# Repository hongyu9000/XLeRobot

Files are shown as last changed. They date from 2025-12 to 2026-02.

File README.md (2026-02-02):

# [XLeRobot 🤖](https://xlerobot.readthedocs.io/en/latest/index.html)




<a href="https://xlerobot.readthedocs.io/en/latest/index.html">
  front
</a>





---

**🚀 Bringing Embodied AI to Everyone - Cheaper Than an iPhone! 📱**  
**💵 Starts from $660 cost and ⏰ <4hrs total assembly time!!**

*Built upon the giants: [LeRobot](https://github.com/huggingface/lerobot), [SO-100/SO-101](https://github.com/TheRobotStudio/SO-ARM100), [Lekiwi](https://github.com/SIGRobotics-UIUC/LeKiwi), [Bambot](https://github.com/timqian/bambot)*

<table>
  <tr>
    <td></td>
    <td></td>
    <td></td>
  </tr>
  <tr>
    <td></td>
    <td></td>
    <td></td>
  </tr>
  <tr>
    <td></td>
    <td></td>
    <td></td>
  </tr>
</table>

---

# 📰 News 
- 2026-1-29: Play with XLeRobot directly in browser with Mujoco and 3DGS: https://vector-wangel.github.io/MuJoCo-GS-Web/
  - 
- 2025-12-02: [Dual-wheel version released](https://xlerobot.readthedocs.io/en/latest/hardware/getting_started/assemble_2wheel.html)! Have a more stable and accurate differential-wheel base for a cheaper price. (Default servo motor, optional scooter brushless Motor available at a similar price)
  

- 2025-11-11: **[Temporary VLA tutorial](https://xlerobot.readthedocs.io/en/latest/software/getting_started/RL_VLA.html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)** out. Official version out soon.
- 2025-09-22: **Hardware Assembly Video Tutorial** availabe at [Youtube](https://www.youtube.com/watch?v=upB1CEFeOlk) and [Bilibili](https://www.bilibili.com/video/BV1AGWFzUEJf/). Thanks WOWROBO for making this video!
- 2025-09-09: **Developer Assembly kit (excluding battery and IKEA cart) ready for purchase** in [China (Taobao) for **3699￥**](https://e.tb.cn/h.SZFbBgZABZ8zRPe?tk=ba514rTBRjQ) and [world-wide for **579\$**](https://shop.wowrobo.com/products/xlerobot-dual-arm-mobile-household-robot-kit?variant=47297659961561). _(In collaboration with **Wowrobo**)_
  - Non-profit, I personally don't earn any from this. I also asked Wowrobo to set the price as low as possible.
  - This is only the assembly kit for developers, please check documentation website and this repo for available codes and tutorials before you purchase.
- 2025-09-09: Joined [Embodied AI Home Robot Hackathon](https://www.seeedstudio.com/embodied-ai-worldwide-hackathon-home-robot.html) (Oct 25–26, Bay Area) held by **SEEED x Nvidia x Huggingface** as mentor! [Register HERE](https://docs.google.com/forms/d/e/1FAIpQLSdYYDegdgIypxuGJNLcoc8kbdmU4jKgl49zg4X-107LAmBN4g/viewform).

- 2025-08-30: XLeRobot 0.3.0 Release with final outfit touch up and household chores showcase demos. 

- 2025-07-30: [Control XLeRobot in real life](https://xlerobot.readthedocs.io/en/latest/software/index.html) with **keyboard/Xbox controller/Switch joycon** in the wild anywhere. All bluetooth, no wifi needed and zero latency.

- 2025-07-08: [**Simulation**](https://xlerobot.readthedocs.io/en/latest/simulation/index.html) with updated urdfs, control scripts (support Quest3 VR, keyboard, Xbox controller, switch joycon), support for new hardware and cameras, RL environment. Get started in 15 min.
-  vr

- 2025-07-01: [**Documentation** website](https://xlerobot.readthedocs.io/en/latest/index.html) out for more orgainized tutorials, demos and resources.

- 2025-06-13: [**XLeRobot 0.2.0**](https://xlerobot.readthedocs.io) hardware setup, the 1st version fully capable for autonomous household tasks, starts from 660$. 

---

## 💵 Total Cost 💵

> [!NOTE] 
> Cost excludes 3D printing, tools, shipping, and taxes.

| Price (Buy all the parts yourself) | US | EU | CN | IN |
| --- | --- | --- | --- | --- |
| **Basic** (use your laptop, single RGB head cam) | **~$660** | **~€680** | **~¥3999** | **~₹87000** |
| ↑ Stereo dual-eye RGB head cam | +$30 | +€30 | +¥199 | +₹6550 |
| + RasberryPi | +$79 | +€79 | +¥399 | +₹7999 |
| ↑ RealSense RGBD head cam | +$220 | +€230 | +¥1499 | +₹35726 |

---
## 🚀 Get Started 🚀

> [!NOTE] 
> If you are totally new to programming, please spend at least a day to get yourself familiar with basic Python, Ubuntu and Github (with the help of Google and AI). At least you should know how to setup ubuntu system, git clone, pip install, use intepreters (VS Code, Cursor, Pycharm, etc.) and directly run commands in the terminals.

1. 💵 **Buy your parts**: [Bill of Materials](https://xlerobot.readthedocs.io/en/latest/hardware/getting_started/material.html)
2. 🖨️ **Print your stuff**: [3D printing](https://xlerobot.readthedocs.io/en/latest/hardware/getting_started/3d.html)
3. 🔨 ~~Avengers~~: [**Assemble**!](https://xlerobot.readthedocs.io/en/latest/hardware/getting_started/assemble.html)
4. 💻 **Software**: [Get your robot moving!](https://xlerobot.readthedocs.io/en/latest/software/index.html)

---

## Contribute

**👋 Want to contribute to XLeRobot?**
Please refer to [CONTRIBUTING.md](CONTRIBUTING.md) for guidance on how to get involved!

**Main Contributors**

- [Gaotian/Vector Wang](https://vector-wangel.github.io/)
- [Jiahao Wang](https://github.com/kahowang), [Chunbo Pan](https://github.com/IIMFINE), [QiLiu](https://github.com/Lakesenberg), [Isaac Sin](https://github.com/IsaacSinn), [Ryan Chan](https://github.com/RapidCAMO): [MakerMods team](https://www.makermods.ai/), VLA and VR integration
- [Zhuoyi Lu](https://lzhuoyi.github.io/Zhuoyi_Lu.github.io/): RL sim2real deploy, teleop on real robot (Xbox, VR, Joycon)
- Yiyang Huang: RL & VLA implementation (ongoing)
- YCP: WebUI for remote control (ongoing)
- [Lixing Zhang](lixingzhang.com): Hardware design improvements
- Nicole Yue: Documentation website setup
- Yuesong Wang: Mujoco simulation
- 

This is just a small brick in the pyramid, made possible by [LeRobot](https://github.com/huggingface/lerobot), [SO-100](https://github.com/TheRobotStudio/SO-ARM100), [Lekiwi](https://github.com/SIGRobotics-UIUC/LeKiwi), and [Bambot](https://github.com/timqian/bambot). Thanks to all the talented contributors behind these detailed and professional projects.

Looking forward to collaborating with anyone interested in contributing to this project!

## About me

[Gaotian/Vector Wang](https://vector-wangel.github.io/)

I am a CS graduate student at Rice University [RobotPi Lab](https://robotpilab.github.io/), focusing on robust object manipulation, where we propse virtual cages and funnels and physics-aware world models to close the Sim2real gap and achieve robust manipulation under uncertainties. One of my papers, Caging in Time, has recently been accepted by International Journal of Robotics Research (IJRR).

I built XLeRobot as a personal hobby to instantiate my research theory, also to provide a low-cost platform for people who are interested in robotics and embodied AI to work with. 

---

## Citation

If you want, you can cite this work with:

```bibtex
@misc{wang2025xlerobot,
    author = {Wang, Gaotian and Lu, Zhuoyi and Yiyang, Huang and Yihao, Liu},
    title = {XLeRobot: A Practical Low-cost Household Dual-Arm Mobile Robot Design for General Manipulation},
    howpublished = "\url{https://github.com/Vector-Wangel/XLeRobot}",
    year = {2025}
}
```
---Generated Image August 27, 2025 - 4_58PM

## 🪧 Disclaimer 🪧

> [!NOTE]
> If you build, buy, or develop a XLeRobot based on this repo, you will be fully responsible for all the physical and mental damages it does to you or others.

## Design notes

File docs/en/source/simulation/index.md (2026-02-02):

# Simulation

##### Web Mujoco simulation

Play with XLeRobot instantly on web, using mujoco engine and 3DGS. See detailed instruction [HERE](https://github.com/Vector-Wangel/MuJoCo-GS-Web)

<iframe 
    src="https://vector-wangel.github.io/MuJoCo-GS-Web/" 
    width="100%" 
    height="600px"
    style="border: none; border-radius: 8px;"
    allowfullscreen>
</iframe>

##### [👋 Get Started](getting_started/index)

- [A short technical blog](https://vectorwang.notion.site/Analytical-IK-for-SO101-20abb280f59380d288bcdd398ffbfab1) for analytical IK introduction.

- A detailed [**Step-by-step Installation Guide**](getting_started/index) that can get you started to replicate this demo in 10 min.

- URDF files, maniskill robot agent scripts, joint/EE control scripts.

##### [👀 VR Control](getting_started/vr_sim)

<video width="100%" style="max-width: 100%;" controls>
  <source src="https://vector-wangel.github.io/XLeRobot-assets/videos/Sim_demos/XLeRobot_0_2_3.mp4" type="video/mp4">
  Your browser does not support the video tag.
</video>

##### [🔩 More Scenes](getting_started/simdemos)

<video width="100%" style="max-width: 100%;" controls>
  <source src="https://vector-wangel.github.io/XLeRobot-assets/videos/Sim_demos/XLeRobot_0_1_5.mp4" type="video/mp4">
  Your browser does not support the video tag.
</video>

```{toctree}
getting_started/index
getting_started/vr_sim
getting_started/simdemos
```

<!-- ```{toctree}
:maxdepth: 1

control/index
table_top_gripper/index
quadruped/index
humanoid/index
mobile_manipulation/index
dextrous/index
digital_twins/index
drawing/index
external/index
``` -->

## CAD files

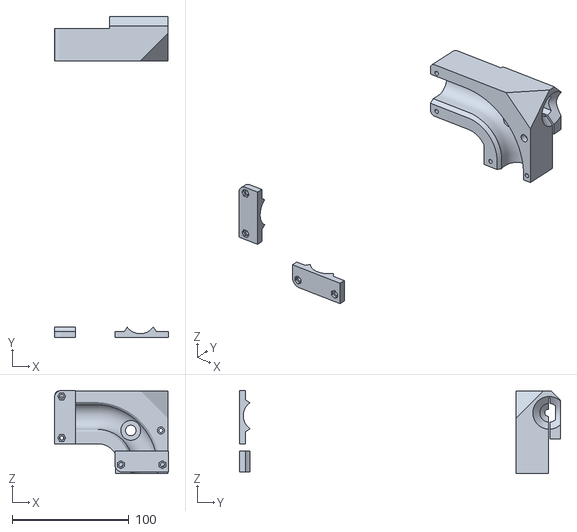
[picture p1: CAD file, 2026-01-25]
hardware/Brushlessmotor connector.stl
98.1 x 275.3 x 71.3

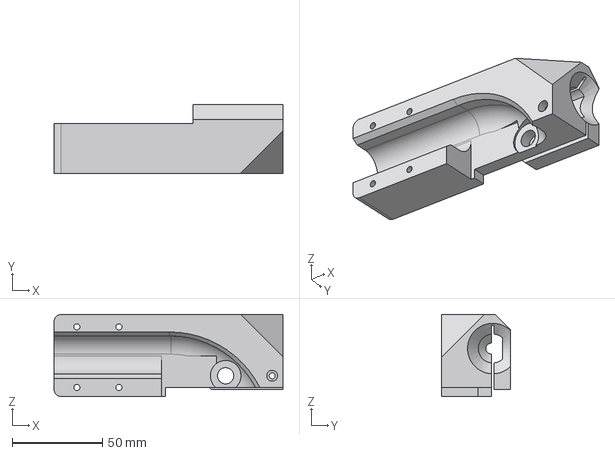
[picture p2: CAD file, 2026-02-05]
hardware/step/brushless_motor_base_holder.step
127.0 x 38.0 x 45.5 mm

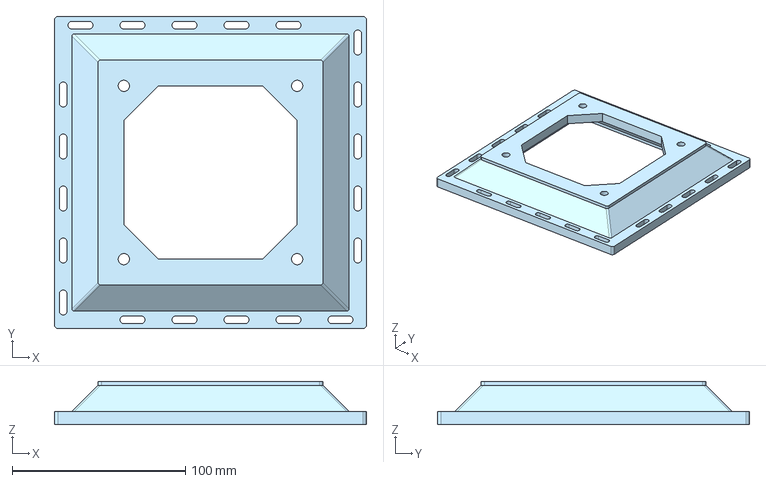
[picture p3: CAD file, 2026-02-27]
hardware/step/HighTorqueRobotics/ht_holder_single.step
180.0 x 180.0 x 25.0 mm

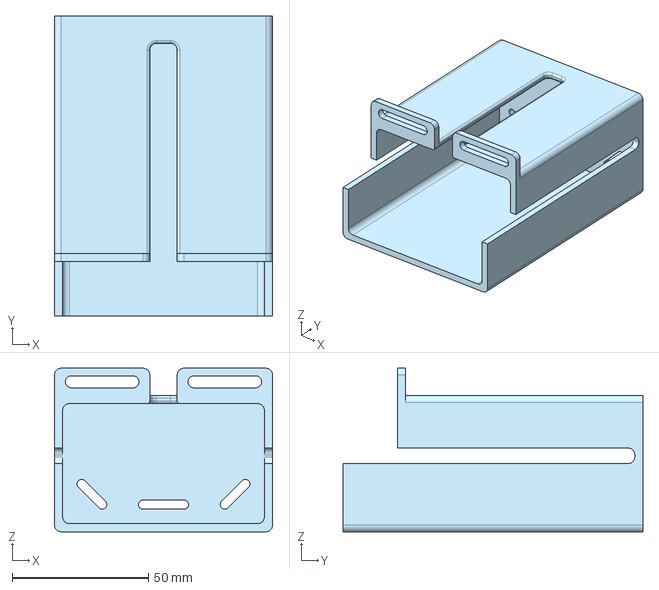
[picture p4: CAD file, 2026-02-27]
hardware/step/Misc/front_back_hub.step
80.0 x 110.0 x 60.0 mm

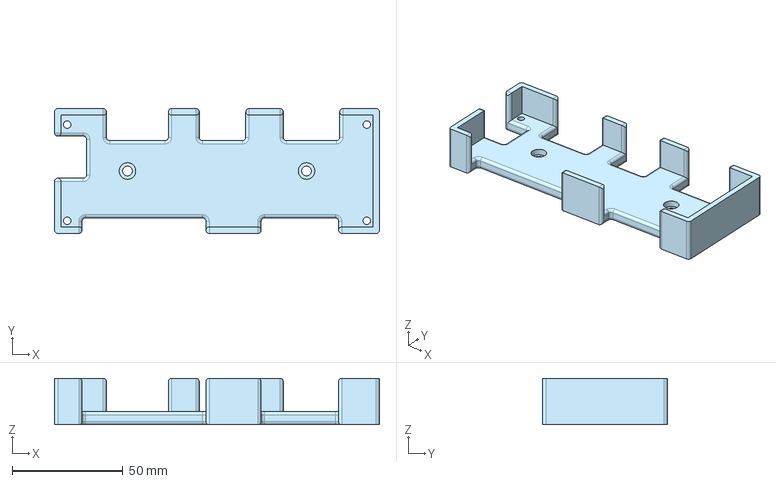
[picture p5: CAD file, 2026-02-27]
hardware/step/ODrive/odrive_cap.step
147.0 x 56.5 x 21.0 mm

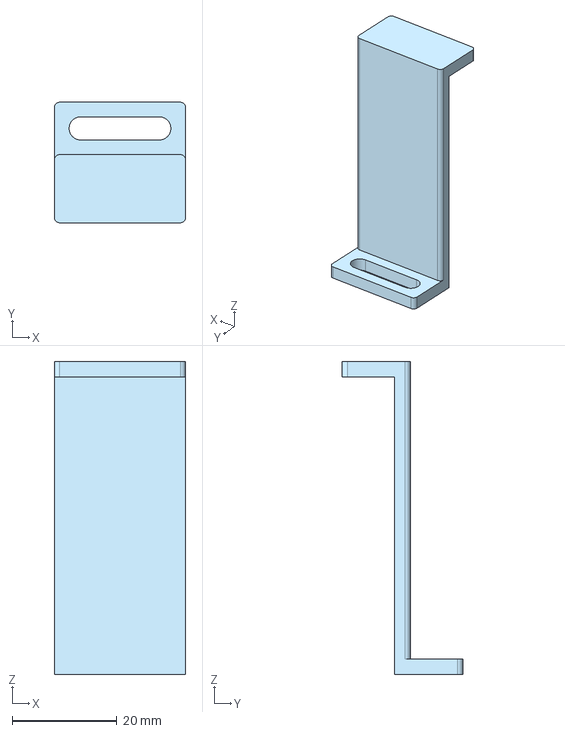
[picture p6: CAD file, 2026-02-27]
hardware/step/Thor/thor_holder_edge.step
25.0 x 23.0 x 59.7 mm

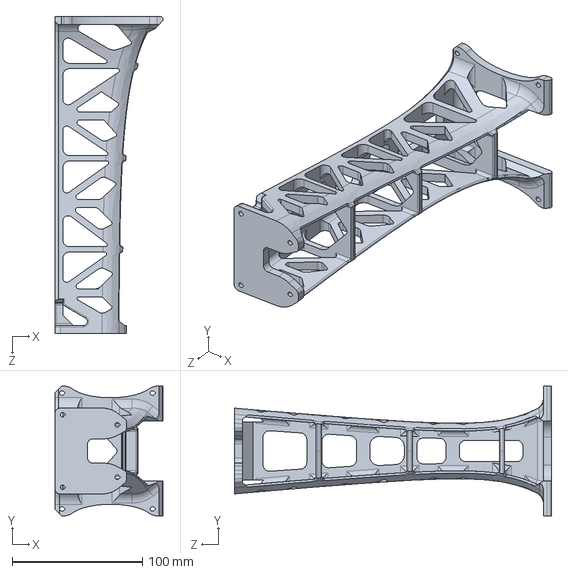
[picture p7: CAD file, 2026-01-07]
hardware/step/XLeRobot_040/XLeRobot040_neck_refined.step
83.1 x 99.8 x 243.8 mm

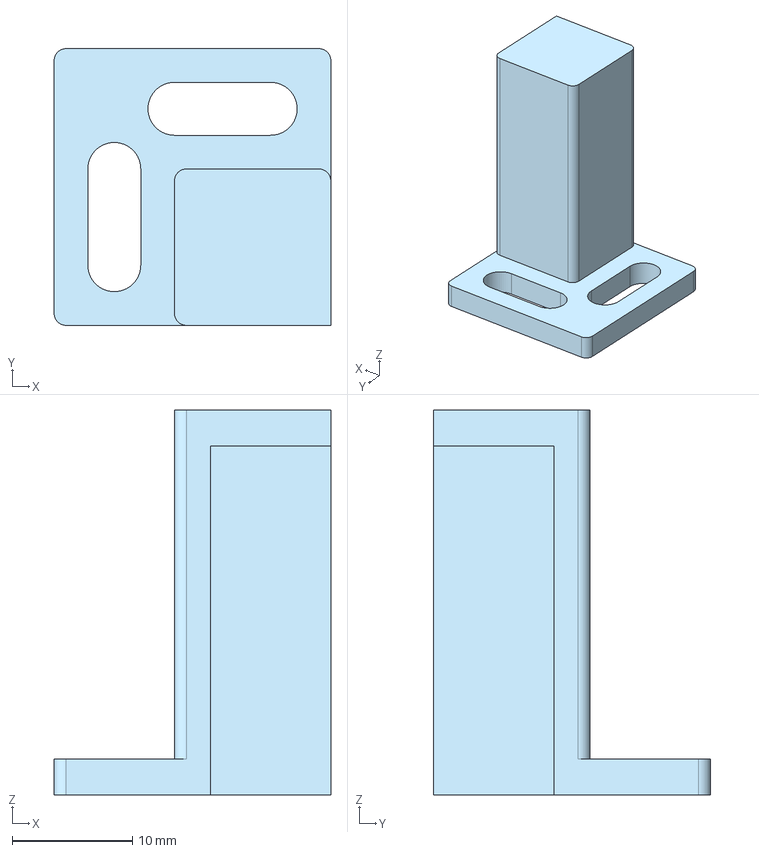
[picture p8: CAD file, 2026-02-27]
hardware/step/HighTorqueRobotics/ht_board_holder_corner.step
23.0 x 23.0 x 32.0 mm

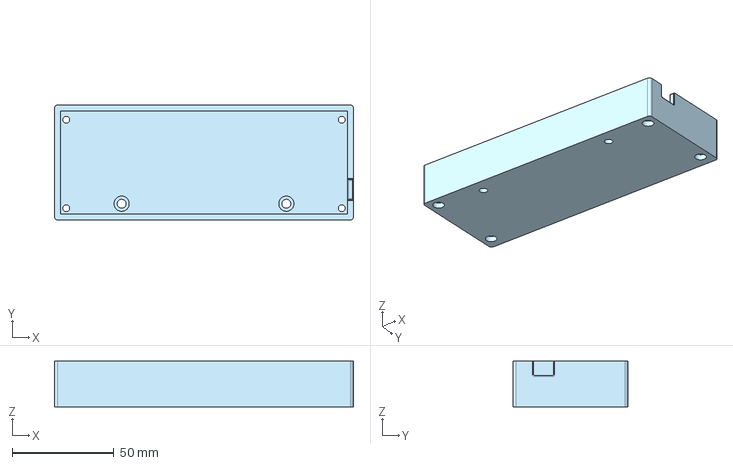
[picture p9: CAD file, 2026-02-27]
hardware/step/ODrive/odrive_housing.step
147.0 x 56.5 x 22.5 mm

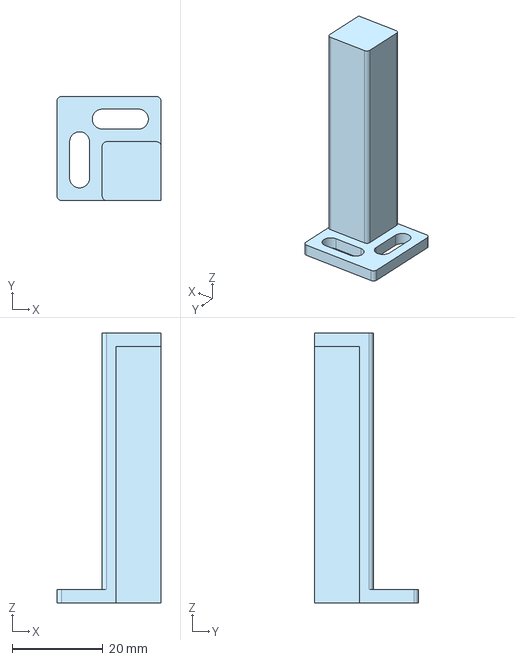
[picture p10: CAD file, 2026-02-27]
hardware/step/Thor/thor_holder_corner.step
23.0 x 23.0 x 59.7 mm

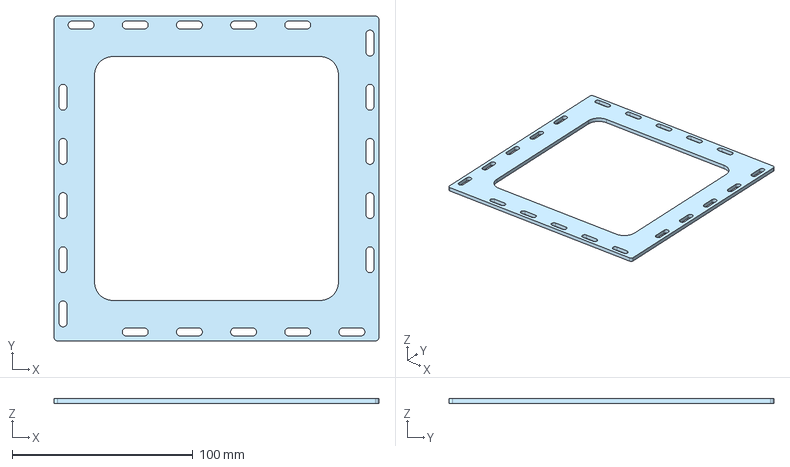
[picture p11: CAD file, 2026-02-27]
hardware/step/HighTorqueRobotics/ht_holder_single_bottom.step
180.0 x 180.0 x 3.00 mm

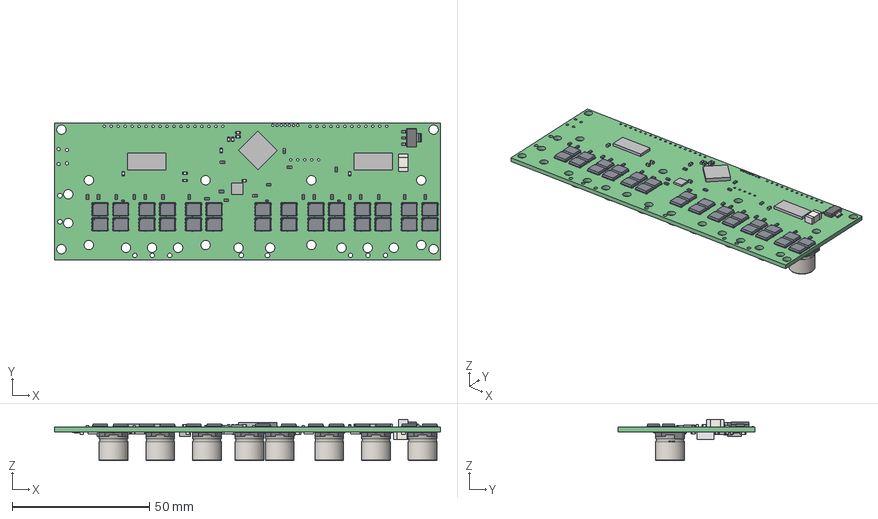
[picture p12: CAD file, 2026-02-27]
hardware/step/ODrive/PCB_v3.2.step
140.5 x 50.0 x 15.0 mm
Board
SOT23-5
Extruded x 201
RES_0402_(1005_metric) x 3
RES_0603_(1608_metric) x 48
SOT223-4
User_Library-DFN5x6_SO8FL_Extruded x 56
User_Library-DFN5x6_SO8FL_Extruded_2 x 56
User_Library-DFN5x6_SO8FL_Cylinder x 28
User_Library-DFN5x6_SO8FL_Extruded_3 x 28
User_Library-DFN5x6_SO8FL_Extruded_4 x 28
User_Library-DFN5x6_SO8FL_Extruded_5 x 112
User_Library-DFN5x6_SO8FL_Extruded_6 x 28
CAP_Alum_Elec_Size_G x 8

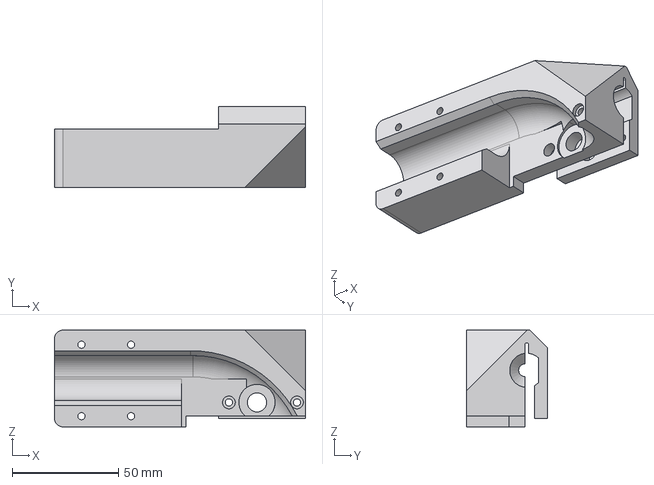
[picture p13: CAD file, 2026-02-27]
hardware/step/ODrive/odrive_motor_holder.step
118.0 x 38.0 x 45.5 mm

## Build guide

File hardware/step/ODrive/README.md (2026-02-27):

ODrive housing parts.

Dimensions retrieved from PCB v3.2.step by https://discourse.odriverobotics.com/t/housing-for-odrive-v3/97.

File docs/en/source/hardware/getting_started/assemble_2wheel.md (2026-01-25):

# Dual wheel Assembly

Here briefly introduce how to build the dual wheel version.

(This page is still under construction)

## Intro
Main changes compared to 0.3.0:

- Dual wheel: More stable, higher moving speed, better passability, and larger torque (compared to 3 omni-wheels). 2 verisons: servo motors and brushless motors.
- Improved top base design: modular arm base with changable arm installing directions. 360 degree and compact head design.  

This 0.4.0 version of XLeRobot is the last version that is fully based on Feetech servo motors and the SO101 chassis. After extensive testing and research, we realized the limitations of servo motors (speed, noise, payload, etc.), and we believe this hardware version offers the best balance among cost, ease of assembly, stability, and practicality.

Regarding a lifting (height-adjustable) base, we have also explored related designs, but the maintenance difficulty and stability issues make it hard to achieve a good solution using only servo motors. For most development scenarios, mobility at desk height is already sufficient to support initial research and development needs. We also found that adding more degrees of freedom increases the difficulty of data collection and hurts policy generalization.

Going forward, we plan to collaborate with Hightorque and wowrobo to build more product-level, low-cost, open-source mobile robots based on higher-performance motors.

Official Assembly Videos from Wowrobo:
<iframe width="800" height="600" 
    src="https://www.youtube.com/embed/4bXCFw57T60" 
    frameborder="0" 
    allowfullscreen>
</iframe>

<iframe width="800" height="600" 
    src="//player.bilibili.com/player.html?bvid=BV1JpiqBfEuf&autoplay=0" 
    frameborder="0" 
    allowfullscreen>
</iframe>

### Servo motor version

Pros: 
- Compared to previous version: more stable, control is more accurate, less wiggle
- Compared to brushless version: still same servo motors, easier wiring and control

Cons:
- Compared to previous version: lose one Dof of moving left and right
- Compared to brushless version: still same servo motors, noisy, speed and torque not very high.

This can already be purchased at wowrobo. 

You can also buy parts yourself, what you need besides 3D printed parts and servo motors:

- Universal walker wheels (5 inches)
- 30 x 37 x 4mm Bearings
- longer Motor cables (or extension kit)



Find STL file [Here](https://github.com/Vector-Wangel/XLeRobot/blob/main/hardware/XLeRobot_0_4_0_extra.stl)

Animation (19)
Animation (18)

Assembled picture:



### Brushless motor version

Build upon [Bracket Bot](https://www.bracket.bot/).

Find the connector to the IKEA cart [here](https://github.com/Vector-Wangel/XLeRobot/blob/main/hardware/Brushlessmotor%20connector.stl). (M8x20 screws required)

Pros: a fully stable and robust version with great performance.

Cons: more complex wiring.



Animation (20)

Still working on, release soon.

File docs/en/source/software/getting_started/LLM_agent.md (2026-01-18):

## LLM Agent Control

Imagine telling the robot "go cleanup my kitchen" and watching it doing so. This tutorial will show you how you can make your XLeRobot fully autonomous, self-decision making machine by providing it with LLM agent. An agent that uses camera vision and voice commands to move the robot and manipulate objects with VLA policies.

Demo of agent controlling XLeRobot, that has a task to grab a notebook and give it to human:

<video width="100%" controls>
  <source src="https://vector-wangel.github.io/XLeRobot-assets/videos/Real_demos/agent_in_action.mov" type="video/mp4">
  Your browser does not support the video tag.
</video>

### Getting Started

To create our agent, we will use the [RoboCrew](https://github.com/Grigorij-Dudnik/RoboCrew) library - one specially designed for embodied agents. On your control device (Raspberry Pi or laptop) create a new virtual environment and install it with:

```bash
pip install robocrew
```

Next, create the python script to control your robot. Let's start by creating a simple agent that performs just one hardcoded task and finishes. 

First, let's initialize camera and create tools for agent to control a wheel movement:

```python
from robocrew.core.camera import RobotCamera
from robocrew.core.LLMAgent import LLMAgent
from robocrew.robots.XLeRobot.tools import create_move_forward, create_turn_right, create_turn_left
from robocrew.robots.XLeRobot.servo_controls import ServoControler

# set up main camera
main_camera = RobotCamera("/dev/camera_center") # camera usb port Eg: /dev/video0

#set up servo controler
right_arm_wheel_usb = "/dev/arm_right"    # provide your right arm usb port. Eg: /dev/ttyACM1
servo_controler = ServoControler(right_arm_wheel_usb=right_arm_wheel_usb)

#set up tools
move_forward = create_move_forward(servo_controler)
turn_left = create_turn_left(servo_controler)
turn_right = create_turn_right(servo_controler)
```

in place of `/dev/arm_right` you should provide the USB port name of your right arm (one connected to the wheels).

Next, let's initialize and run an agent itself:

```python
# init agent
agent = LLMAgent(
    model="google_genai:gemini-3-flash-preview",
    tools=[
        move_forward,
        turn_left,
        turn_right,
    ],
    main_camera=main_camera,
    servo_controler=servo_controler,
)

agent.task = "Approach a human."

agent.go()
```

In the code above we initialized our agent with the maneuver tools we created earlier. You can provide any model in LangChain notation. Next, we hard-coding a task for our agent and running it.

Before going to LLM, camera image is specially augmented to make it easier for robot to understand its environment: 

<div style="text-align: center; font-style: italic">
  
  <p>That's how your robot sees the world.</p>
</div>

Also, create the `.env` file with parameter `GOOGLE_API_KEY=<your gemini api key here>` beside the script to connect to LLM.

Now run the code and watch your XLeRobot approaching you - then it will finish its work by calling `finish_task` tool!

Complete code is here:

```python
from robocrew.core.camera import RobotCamera
from robocrew.core.LLMAgent import LLMAgent
from robocrew.robots.XLeRobot.tools import create_move_forward, create_turn_right, create_turn_left
from robocrew.robots.XLeRobot.servo_controls import ServoControler

# set up main camera
main_camera = RobotCamera("/dev/camera_center") # camera usb port Eg: /dev/video0

#set up servo controler
right_arm_wheel_usb = "/dev/arm_right"    # provide your right arm usb port. Eg: /dev/ttyACM1
left_arm_head_usb = "/dev/arm_left"      # provide your left arm usb port. Eg: /dev/ttyACM0
servo_controler = ServoControler(right_arm_wheel_usb, left_arm_head_usb)

#set up tools
move_forward = create_move_forward(servo_controler)
turn_left = create_turn_left(servo_controler)
turn_right = create_turn_right(servo_controler)

# init agent
agent = LLMAgent(
    model="google_genai:gemini-3-flash-preview",
    tools=[move_forward, turn_left, turn_right],
    main_camera=main_camera,
    servo_controler=servo_controler,
)

agent.task = "Approach a human."

agent.go()
```

### Set up Udev rules

Before proceeding to more advanced examples, let's do optional, but highly recommended step - make the usb port names for arms and cameras constant, to avoid swapping those names after every Raspberry Pi reboot. To do it, we need to set up udev rules. Luckily, RoboCrew already contains an utility that makes a complicated process of setting up udevs a matter of few clicks.

Run:

```bash
robocrew-setup-usb-modules
```

Utility will ask you to disconnect all usbs and then connect one after another - that way your usb devices will receive a constant names.

### Voice-conrolled agent

We managed to run our simple agent, now let's give it an ability to listen to our voice commands through the microphone.

First, we need to install Portaudio, to enable our control device to hear:

```bash
sudo apt install portaudio19-dev
```

Connect to your agent a soundcard with microphone, and optionally speaker, if you want robot to respond to you.

Let's change the agent initialization a little bit:

```python
agent = LLMAgent(
    model="google_genai:gemini-3-flash-preview",
    tools=[move_forward, turn_left, turn_right],
    main_camera=main_camera,
    servo_controler=servo_controler,
    sounddevice_index=2,    # provide your microphone device index.
    wakeword="hey robot",   # optional - set up custom wakeword (default is "robot")
    tts=True,               # enable text-to-speech (robot can speak).
)

agent.go()
```

As you can see, we need to provide index of our soundcard with microphone. We can also set up a wakeword (default is "robot") - when robot hears that word in your sentence, it treats sentence as a new task; otherwise ignores it.

`tts=True` is needed if you want robot to speak.

We can also set up `history_len` - how many of last movements robot should keep in the memory, to avoid memory overflow.

Run the code and ask the robot to go somewhere!

Complete code is here:

```python
from robocrew.core.camera import RobotCamera
from robocrew.core.LLMAgent import LLMAgent
from robocrew.robots.XLeRobot.tools import create_move_forward, create_turn_right, create_turn_left
from robocrew.robots.XLeRobot.servo_controls import ServoControler

# set up main camera
main_camera = RobotCamera("/dev/camera_center") # camera usb port Eg: /dev/video0

#set up servo controler
right_arm_wheel_usb = "/dev/arm_right"    # provide your right arm usb port. Eg: /dev/ttyACM1
servo_controler = ServoControler(right_arm_wheel_usb=right_arm_wheel_usb)

#set up tools
move_forward = create_move_forward(servo_controler)
turn_left = create_turn_left(servo_controler)
turn_right = create_turn_right(servo_controler)

# init agent
agent = LLMAgent(
    model="google_genai:gemini-3-flash-preview",
    tools=[move_forward, turn_left, turn_right],
    main_camera=main_camera,
    servo_controler=servo_controler,
    sounddevice_index=2,    # provide your microphone device index.
    wakeword="hey robot",   # optional - set up custom wakeword (default is "robot")
    tts=True,               # enable text-to-speech (robot can speak).
)

agent.task = "Wait for the voice commands and execute."

agent.go()
```

### Activate arm manipulation

Let's go to the most advanced and useful part of our agent - the arms manipulation through VLA policies! That allows the robot to make full range of household tasks - like throwing out a trash or bringing you a tea from kitchen.

First of all, you need to train the policy agent will utilize later. Reference [VLA tutorial](https://xlerobot.readthedocs.io/en/latest/software/getting_started/VLA_ACT.html) to learn how to do it.

Let's assume you trained VLA policy that grabs a notebook from the table and put it in the robot basket (for further transportation). Let's add it as a tool for your agent:

```python
from robocrew.robots.XLeRobot.tools import create_vla_single_arm_manipulation

pick_up_notebook = create_vla_single_arm_manipulation(
    tool_name="Grab_a_notebook",
    tool_description="Manipulation tool to grab a notebook from the table and put it to your basket.",
    task_prompt="Grab a notebook.",
    server_address="0.0.0.0:8080",
    policy_name="Grigorij/act_right-arm-grab-notebook-2",
    policy_type="act",
    arm_port=right_arm_wheel_usb,
    servo_controler=servo_controler,
    camera_config={"main": {"index_or_path": "/dev/camera_center"}, "right_arm": {"index_or_path": "/dev/camera_right"}},
    main_camera_object=main_camera,
    policy_device="cpu",
)
```

Provide the tool with parameters your custom tool name and description - that's what LLM will see. Also, provide VLA-related parameters - as the name of your trained policy on HF hub, policy type, camera config (same you used during dataset collection).

Then add created `pick_up_notebook` tool to the tools of your agent. You can create as many manipulation tools as you want.

Our tool is a policy client, but all VLA computations are run on the server side. We need to run policy server - on Raspberry Pi only in case of light-weight ACT policy, on different computer for all other policies. Run your server with:

```
python -m lerobot.async_inference.policy_server \
     --host=0.0.0.0 \
     --port=8080
```

In case you using external computer in your local network as a server, provide its IP instead of zeros to `server_address` parameter like: `server_address="123.234.12.34:8080"`

That's it! Prompt your robot to grab a notebook from the table and give it to you!

In the full code, we also added more movement tools for more precision navigation:

```python
from robocrew.core.camera import RobotCamera
from robocrew.core.LLMAgent import LLMAgent
from robocrew.robots.XLeRobot.tools import \
    create_vla_single_arm_manipulation, \
    create_go_to_precision_mode, \
    create_go_to_normal_mode, \
    create_move_backward, \
    create_move_forward, \
    create_strafe_right, \
    create_strafe_left, \
    create_look_around, \
    create_turn_right, \
    create_turn_left
from robocrew.robots.XLeRobot.servo_controls import ServoControler

# set up main camera
main_camera = RobotCamera("/dev/camera_center") # camera usb port Eg: /dev/video0

#set up servo controler
right_arm_wheel_usb = "/dev/arm_right"    # provide your right arm usb port. Eg: /dev/ttyACM1
left_arm_head_usb = "/dev/arm_left"      # provide your left arm usb port. Eg: /dev/ttyACM0
servo_controler = ServoControler(right_arm_wheel_usb, left_arm_head_usb)

#set up tools
move_forward = create_move_forward(servo_controler)
move_backward = create_move_backward(servo_controler)
turn_left = create_turn_left(servo_controler)
turn_right = create_turn_right(servo_controler)
strafe_left = create_strafe_left(servo_controler)
strafe_right = create_strafe_right(servo_controler)

look_around = create_look_around(servo_controler, main_camera)
go_to_precision_mode = create_go_to_precision_mode(servo_controler)
go_to_normal_mode = create_go_to_normal_mode(servo_controler)

pick_up_notebook = create_vla_single_arm_manipulation(
    tool_name="Grab_a_notebook",
    tool_description="Manipulation tool to grab a notebook from the table and put it to your basket.",
    task_prompt="Grab a notebook.",
    server_address="0.0.0.0:8080",
    policy_name="Grigorij/act_right-arm-grab-notebook-2",
    policy_type="act",
    arm_port=right_arm_wheel_usb,
    servo_controler=servo_controler,
    camera_config={"main": {"index_or_path": "/dev/camera_center"}, "right_arm": {"index_or_path": "/dev/camera_right"}},
    main_camera_object=main_camera,
    policy_device="cpu",
)

give_notebook = create_vla_single_arm_manipulation(
    tool_name="Give_a_notebook_to_a_human",
    tool_description="Manipulation tool to take a notebook from your basket and give it to human.",
    task_prompt="Grab a notebook and give it to a human.",
    server_address="0.0.0.0:8080",
    policy_name="Grigorij/act_right_arm_give_notebook",
    policy_type="act",
    arm_port=right_arm_wheel_usb,
    servo_controler=servo_controler,
    camera_config={"main": {"index_or_path": "/dev/camera_center"}, "right_arm": {"index_or_path": "/dev/camera_right"}},
    main_camera_object=main_camera,
    policy_device="cpu",
    execution_time=45,
)

# init agent
agent = LLMAgent(
    model="google_genai:gemini-3-flash-preview",
    system_prompt=system_prompt,
    tools=[
        move_forward,
        move_backward,
        strafe_left,
        strafe_right,
        turn_left,
        turn_right,
        look_around,
        go_to_precision_mode,
        go_to_normal_mode,
        pick_up_notebook,
        give_notebook,
    ],
    history_len=8,
    main_camera=main_camera,
    camera_fov=90,
    servo_controler=servo_controler,
    debug_mode=True,
)

agent.task = "Approach blue notebook, grab it from the table and give it to human. Do not approach human until you grabbed a notebook."

agent.go()
```

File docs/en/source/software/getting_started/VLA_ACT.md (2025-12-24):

## VLA (ACT)

Single arm VLA policy implementation on XLeRobot:

<video width="100%" controls>
  <source src="https://vector-wangel.github.io/XLeRobot-assets/videos/Real_demos/Act_on_RPi_Xle.mp4" type="video/mp4">
  Your browser does not support the video tag.
</video>

# Vision-Language-Action (VLA) Training for XLeRobot

This tutorial will guide you through the process of training a Vision-Language-Action (VLA) model to control your XLeRobot arms autonomously. As control devices we will use VR and leader arm. If you want us to add more control devices (as xbox controller or keyboard) feel free to open an issue.

## What You'll Learn

1. How to teleoperate and record demonstration datasets for XLeRobot
2. How to train and evaluate your policy
3. How to make the policy work effectively

By following these steps, you'll be able to train your XLeRobot to autonomously perform various household tasks using LeRobot policies (such as ACT), including picking up objects, wiping tables, or organizing items.

---

## 1. Hardware Setup and Check

### 1.1 Turn the head camera to an appropriate angle

For both VLA dataset collection and inference you need to keep consistent head servos angles - otherwise policy will not work or performance will drop.

Also, ensure the camera fully sees arms operation field - if for example your policy takes object from table and puts it into robot basket - both table and basket need to be fully visible.

You can turn the camera by your hand or use utility from RoboCrew lib (especially if you want to use your VLA policy as LLM agent tool) - this will provide you with a perfect repeatability of the camera angle:

```python
from robocrew.robots.XLeRobot.servo_controls import ServoControler

servo_controler = ServoControler(left_arm_head_usb='/dev/arm_left')
servo_controler.turn_head_to_vla_position()
```

### 1.2 Check Camera Status

Use the LeRobot [cameras](https://huggingface.co/docs/lerobot/cameras) tutorial to verify your camera setup:

```bash
lerobot-find-cameras opencv  # or use 'realsense' for Intel RealSense cameras
```

You should see output similar to this:

```
--- Detected Cameras ---
Camera #0:
  Name: OpenCV Camera @ 0
  Type: OpenCV
  Id: 0
  Backend api: AVFOUNDATION
  Default stream profile:
    Format: 16.0
    Width: 1920
    Height: 1080
    Fps: 15.0
--------------------
(more cameras ...)
```

XLeRobot has three cameras: two wrist cameras and one head camera. Make sure all three are detected.

---

## 2.1. Record Dataset for a Single Arm Using a Leader Arm

Very often the single arm is enough to perform your pick-and-place task. Using single arm only means using less servos and cameras, so it will be much easier for your model to learn the policy. If your task is simple enough to be done with one arm - let's train policy for it.

Connect a leader arm to the Raspberry Pi or other computer you use to record a dataset.

Following script will start recording:

```bash
python /your_dir/lerobot/src/lerobot/record.py \
  --robot.type=so101_follower \
  --robot.port=/dev/right_arm \
  --robot.id=robot_right_arm \
  --robot.cameras="{ head: {type: intelrealsense, serial_number_or_name: 935422072196, width: 640, height: 480, fps: 30, use_depth: True}, right: {type: opencv, index_or_path: '/dev/video6', width: 640, height: 480, fps: 30}}" \
  --teleop.type=so101_leader \
  --teleop.port=/dev/ttyACM0 \
  --teleop.id=my_leader_arm \
  --display_data=true \
  --dataset.repo_id=your_huggingface_id/clear_table_single_arm \
  --dataset.num_episodes=50 \
  --dataset.single_task="Clear the table"
```

## 2.2. Record Dataset for XLeRobot with VR

For more complicated policies, let's use VR to activate both robot's arms and wheels.

Before the official merge into LeRobot, copy the required code from XLeRobot to LeRobot:
```bash
cp your_dir/XLeRobot/software/src/record.py your_dir/lerobot/src/lerobot/record.py
cp your_dir/XLeRobot/software/src/teleporators/xlerobot_vr your_dir/lerobot/src/lerobot/teleporators/xlerobot_vr -r
```

### Recording Script Example

Run the following script to start recording:

```bash
python /your_dir/lerobot/src/lerobot/record.py \
  --robot.type=xlerobot \
  --robot.cameras="{ head: {type: intelrealsense, serial_number_or_name: 935422072196, width: 640, height: 480, fps: 30, use_depth: True}, right: {type: opencv, index_or_path: '/dev/video6', width: 640, height: 480, fps: 20}, left: {type: opencv, index_or_path: '/dev/video8', width: 640, height: 480, fps: 20} }" \
  --dataset.repo_id=your_huggingface_id/clear_table \
  --dataset.single_task="Clear the table." \
  --dataset.root=your_dir/clear_table \
  --display_data=true \
  --teleop.type=xlerobot_vr
```

### Important Notes

1. **Camera Configuration**: The `robot.cameras` parameter should match the output from section 1.2. If you encounter camera timeout errors, reduce the FPS (e.g., from 30 to 20).

2. **VR Connection**: At the beginning of the script, it will wait for VR connection. Visit the URL displayed in the terminal output using your VR device. Data collection will start automatically once the connection is established.

3. **VR Controls**: The left-hand controller has four functions (practice several times to become familiar):
   - **Reset Position**: Returns the robot arms to their zero position
   - **Early Exit**: Ends the current episode collection (use when you've completed the task)
   - **Delete Episode**: Deletes the current episode (use if the task failed)
   - **Stop Recording**: Stops the dataset recording session

<p align="center">
  
  
</p>

---

```{note}
Some tips for a better performance:

1. **Check for Dropped Frames**: Review [these examples](https://gold-column-7d2.notion.site/Some-examples-for-VLA-dataset-2a2e20e657ad8037aa09d1228a2bf4bf?pvs=73) to understand what dropped frames look like. Monitor your bandwidth and CPU usage during recording. If issues occur, optimize your system accordingly.

2. **Avoid Redundant Frames**: Use the early exit function when the task is completed, rather than letting the script continue logging static robot data.

3. **Maintain Scene Consistency**: Avoid having additional moving objects or people in the camera view during recording.
```
---

## 3. Train a Policy

After collecting your datasets, refer to the LeRobot [training tutorial](https://huggingface.co/docs/lerobot/il_robots#train-a-policy) to select and train a policy.

## 4. Deploy a Model

The simplest way to test your trained model:
```python
python /your_dir/lerobot/src/lerobot/record.py \
  --robot.type=xlerobot \
  --robot.cameras="{ head: {type: intelrealsense, serial_number_or_name: 935422072196, width: 640, height: 480, fps: 30, use_depth: True}, right: {type: opencv, index_or_path: '/dev/video6', width: 640, height: 480, fps: 20}, left: {type: opencv, index_or_path: '/dev/video8', width: 640, height: 480, fps: 20} }" \
  --dataset.repo_id=your_huggingface_id/clear_table \
  --dataset.single_task="Clear the table." \
  --dataset.root=your_dir/clear_table \
  --display_data=true \
  --teleop.type=xlerobot_vr
```

Script above runs policy locally on your robot's Raspberry. For lightweight ACT policy it's enough, but for other more resource-consuming policies, the Raspberry will not provide enough computation. 

To run powerful policies as SmolVLA or PI0,5 we need an external computer with GPU. Follow the Lerobot [async inference guide](https://huggingface.co/docs/lerobot/async) to set up policy server on your PC, and client on the XLeRobot. Use loopback interface (0.0.0.0) instead of localhost for your server, and provide server's local IP to the client.

In most cases you'll want to use your VLA policy not by itself, but as a tool of the [LLM agent](https://xlerobot.readthedocs.io/en/latest/software/getting_started/LLM_agent.html). RoboCrew lib already provides you with async client in the tool. Before using it, remember to run policy server on the server machine:

```
python -m lerobot.async_inference.policy_server \
     --host=0.0.0.0 \
     --port=8080
```

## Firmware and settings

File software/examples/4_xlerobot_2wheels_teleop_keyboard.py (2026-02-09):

# To Run on the host
'''python
PYTHONPATH=src python -m lerobot.robots.xlerobot_2wheels.xlerobot_2wheels_host --robot.id=my_xlerobot_2wheels
'''

# To Run the teleop:
'''python
PYTHONPATH=src python -m examples.xlerobot_2wheels.teleoperate_Keyboard
'''

import time
import numpy as np
import math

from lerobot.robots.xlerobot_2wheels import XLerobot2WheelsClient, XLerobot2WheelsClientConfig, XLerobot2WheelsConfig, XLerobot2Wheels
# from lerobot.utils.robot_utils import busy_wait
from lerobot.utils.robot_utils import precise_sleep
from lerobot.utils.visualization_utils import init_rerun, log_rerun_data
from lerobot.model.SO101Robot import SO101Kinematics
from lerobot.teleoperators.keyboard.teleop_keyboard import KeyboardTeleop, KeyboardTeleopConfig

# Base speed control parameters - adjustable slopes
BASE_ACCELERATION_RATE = 10.0  # acceleration slope (speed/second)
BASE_DECELERATION_RATE = 10  # deceleration slope (speed/second) - very slow for noticeable deceleration
BASE_MAX_SPEED = 6.0          # maximum speed multiplier
MIN_VELOCITY_THRESHOLD = 0.02 # minimum velocity to send to motors during deceleration

# Keymaps (semantic action: key) - Updated for differential drive
LEFT_KEYMAP = {
    'shoulder_pan+': 'q', 'shoulder_pan-': 'e',
    'wrist_roll+': 'r', 'wrist_roll-': 'f',
    'gripper+': 't', 'gripper-': 'g',
    'x+': 'w', 'x-': 's', 'y+': 'a', 'y-': 'd',
    'pitch+': 'z', 'pitch-': 'x',
    'reset': 'c',
    # For head motors
    "head_motor_1+": "<", "head_motor_1-": ">",
    "head_motor_2+": ",", "head_motor_2-": ".",
    
    'triangle': 'y',  # Rectangle trajectory key
}
RIGHT_KEYMAP = {
    'shoulder_pan+': '7', 'shoulder_pan-': '9',
    'wrist_roll+': '/', 'wrist_roll-': '*',
    'gripper+': '+', 'gripper-': '-',
    'x+': '8', 'x-': '2', 'y+': '4', 'y-': '6',
    'pitch+': '1', 'pitch-': '3',
    'reset': '0',

    'triangle': 'Y',  # Rectangle trajectory key
}

LEFT_JOINT_MAP = {
    "shoulder_pan": "left_arm_shoulder_pan",
    "shoulder_lift": "left_arm_shoulder_lift",
    "elbow_flex": "left_arm_elbow_flex",
    "wrist_flex": "left_arm_wrist_flex",
    "wrist_roll": "left_arm_wrist_roll",
    "gripper": "left_arm_gripper",
}
RIGHT_JOINT_MAP = {
    "shoulder_pan": "right_arm_shoulder_pan",
    "shoulder_lift": "right_arm_shoulder_lift",
    "elbow_flex": "right_arm_elbow_flex",
    "wrist_flex": "right_arm_wrist_flex",
    "wrist_roll": "right_arm_wrist_roll",
    "gripper": "right_arm_gripper",
}

# Head motor mapping
HEAD_MOTOR_MAP = {
    "head_motor_1": "head_motor_1",
    "head_motor_2": "head_motor_2",
}

class RectangularTrajectory:
    """
    Generates a rectangular trajectory on the x-y plane with sinusoidal velocity profiles.
    The rectangle is divided into 4 line segments, each with smooth acceleration/deceleration.
    """
    def __init__(self, width=0.06, height=0.06, segment_duration=0.91):
        """
        Initialize rectangular trajectory parameters.
        
        Args:
            width: Rectangle width in meters
            height: Rectangle height in meters  
            segment_duration: Time for each line segment in seconds
        """
        self.width = width
        self.height = height
        self.segment_duration = segment_duration
        self.total_duration = 4 * segment_duration
        
    def get_trajectory_point(self, current_x, current_y, t):
        """
        Get the target x, y position at time t for the rectangular trajectory.
        
        Args:
            current_x: Starting x position
            current_y: Starting y position
            t: Time since trajectory start (0 to total_duration)
            
        Returns:
            tuple: (target_x, target_y)
        """
        # Determine which segment we're in
        segment = int(t / self.segment_duration)
        segment_t = t % self.segment_duration
        
        # Normalize segment time (0 to 1)
        normalized_t = segment_t / self.segment_duration
        
        # Sinusoidal velocity profile: smooth acceleration and deceleration
        # s(t) = 0.5 * (1 - cos(π * t)) gives smooth 0 to 1 transition
        smooth_t = 0.5 * (1 - math.cos(math.pi * normalized_t))
        
        # Define rectangle corners relative to starting position
        corners = [
            (current_x, current_y),                           # Start (bottom-left)
            (current_x + self.width, current_y),              # Bottom-right
            (current_x + self.width, current_y + self.height), # Top-right  
            (current_x, current_y + self.height),             # Top-left
            (current_x, current_y)                            # Back to start
        ]
        
        # Clamp segment to valid range
        segment = max(0, min(3, segment))
        
        # Interpolate between current corner and next corner
        start_corner = corners[segment]
        end_corner = corners[segment + 1]
        
        target_x = start_corner[0] + smooth_t * (end_corner[0] - start_corner[0])
        target_y = start_corner[1] + smooth_t * (end_corner[1] - start_corner[1])
        
        return target_x, target_y

class SimpleHeadControl:
    def __init__(self, initial_obs, kp=0.81):
        self.kp = kp
        self.degree_step = 1
        # Initialize head motor positions
        self.target_positions = {
            "head_motor_1": initial_obs.get("head_motor_1.pos", 0.0),
            "head_motor_2": initial_obs.get("head_motor_2.pos", 0.0),
        }
        self.zero_pos = {"head_motor_1": 0.0, "head_motor_2": 0.0}

    def move_to_zero_position(self, robot):
        self.target_positions = self.zero_pos.copy()
        action = self.p_control_action(robot)
        robot.send_action(action)

    def handle_keys(self, key_state):
        if key_state.get('head_motor_1+'):
            self.target_positions["head_motor_1"] += self.degree_step
            print(f"[HEAD] head_motor_1: {self.target_positions['head_motor_1']}")
        if key_state.get('head_motor_1-'):
            self.target_positions["head_motor_1"] -= self.degree_step
            print(f"[HEAD] head_motor_1: {self.target_positions['head_motor_1']}")
        if key_state.get('head_motor_2+'):
            self.target_positions["head_motor_2"] += self.degree_step
            print(f"[HEAD] head_motor_2: {self.target_positions['head_motor_2']}")
        if key_state.get('head_motor_2-'):
            self.target_positions["head_motor_2"] -= self.degree_step
            print(f"[HEAD] head_motor_2: {self.target_positions['head_motor_2']}")

    def p_control_action(self, robot):
        obs = robot.get_observation()
        action = {}
        for motor in self.target_positions:
            current = obs.get(f"{HEAD_MOTOR_MAP[motor]}.pos", 0.0)
            error = self.target_positions[motor] - current
            control = self.kp * error
            action[f"{HEAD_MOTOR_MAP[motor]}.pos"] = current + control
        return action

class SimpleTeleopArm:
    def __init__(self, kinematics, joint_map, initial_obs, prefix="left", kp=0.81):
        self.kinematics = kinematics
        self.joint_map = joint_map
        self.prefix = prefix  # To distinguish left and right arm
        self.kp = kp
        # Initial joint positions
        self.joint_positions = {
            "shoulder_pan": initial_obs[f"{prefix}_arm_shoulder_pan.pos"],
            "shoulder_lift": initial_obs[f"{prefix}_arm_shoulder_lift.pos"],
            "elbow_flex": initial_obs[f"{prefix}_arm_elbow_flex.pos"],
            "wrist_flex": initial_obs[f"{prefix}_arm_wrist_flex.pos"],
            "wrist_roll": initial_obs[f"{prefix}_arm_wrist_roll.pos"],
            "gripper": initial_obs[f"{prefix}_arm_gripper.pos"],
        }
        # Set initial x/y to fixed values
        self.current_x = 0.1629
        self.current_y = 0.1131
        self.pitch = 0.0
        # Set the degree step and xy step
        self.degree_step = 3
        self.xy_step = 0.0081
        # Set target positions to zero for P control
        self.target_positions = {
            "shoulder_pan": 0.0,
            "shoulder_lift": 0.0,
            "elbow_flex": 0.0,
            "wrist_flex": 0.0,
            "wrist_roll": 0.0,
            "gripper": 0.0,
        }
        self.zero_pos = {
            'shoulder_pan': 0.0,
            'shoulder_lift': 0.0,
            'elbow_flex': 0.0,
            'wrist_flex': 0.0,
            'wrist_roll': 0.0,
            'gripper': 0.0
        }
        
        # Rectangular trajectory instance
        self.rectangular_trajectory = RectangularTrajectory(
            width=0.06,          # 6cm wide rectangle
            height=0.06,         # 4cm tall rectangle  
            segment_duration=1.01 # 3 seconds per line segment
        )

    def move_to_zero_position(self, robot):
        print(f"[{self.prefix}] Moving to Zero Position: {self.zero_pos} ......")
        self.target_positions = self.zero_pos.copy()  # Use copy to avoid reference issues
        
        # Reset kinematic variables to their initial state
        self.current_x = 0.1629
        self.current_y = 0.1131
        self.pitch = 0.0
        
        # Don't let handle_keys recalculate wrist_flex - set it explicitly
        self.target_positions["wrist_flex"] = 0.0
        
        action = self.p_control_action(robot)
        robot.send_action(action)

    def execute_rectangular_trajectory(self, robot, fps=30):
        """
        Execute a blocking rectangular trajectory on the x-y plane.
        
        Args:
            robot: Robot instance to send actions to
            fps: Control loop frequency
        """
        print(f"[{self.prefix}] Starting rectangular trajectory...")
        print(f"[{self.prefix}] Rectangle: {self.rectangular_trajectory.width:.3f}m x {self.rectangular_trajectory.height:.3f}m")
        print(f"[{self.prefix}] Duration: {self.rectangular_trajectory.total_duration:.3f}s total")
        
        # Store starting position
        start_x = self.current_x
        start_y = self.current_y
        
        # Execute trajectory
        start_time = time.time()
        dt = 1.0 / fps
        
        while True:
            current_time = time.time()
            elapsed_time = current_time - start_time
            
            # Check if trajectory is complete
            if elapsed_time >= self.rectangular_trajectory.total_duration:
                print(f"[{self.prefix}] Rectangular trajectory completed!")
                break
                
            # Get target position from trajectory
            target_x, target_y = self.rectangular_trajectory.get_trajectory_point(
                start_x, start_y, elapsed_time
            )
            
            # Update current position
            self.current_x = target_x
            self.current_y = target_y
            
            # Calculate inverse kinematics
            try:
                joint2, joint3 = self.kinematics.inverse_kinematics(self.current_x, self.current_y)
                self.target_positions["shoulder_lift"] = joint2
                self.target_positions["elbow_flex"] = joint3
                
                # Update wrist_flex coupling
                self.target_positions["wrist_flex"] = (
                    -self.target_positions["shoulder_lift"]
                    -self.target_positions["elbow_flex"]
                    + self.pitch
                )
                
                # Get action
                action = self.p_control_action(robot)
                
                # Determine which arm is executing and send appropriate action structure
                if self.prefix == "left":
                    # Send left arm action with empty actions for other components
                    robot_action = {**action, **{}, **{}, **{}}
                elif self.prefix == "right":
                    # Send right arm action with empty actions for other components
                    robot_action = {**{}, **action, **{}, **{}}
                
                # Send action to robot
                robot.send_action(robot_action)
                
                # Get observation and log data
                obs = robot.get_observation()
                log_rerun_data(obs, robot_action)
                
            except Exception as e:
                print(f"[{self.prefix}] IK failed at x={self.current_x:.4f}, y={self.current_y:.4f}: {e}")
                break
                
            # Maintain control frequency
            # busy_wait(dt)
        
        print(f"[{self.prefix}] Trajectory execution finished.")

    def handle_keys(self, key_state):
        # Joint increments
        if key_state.get('shoulder_pan+'):
            self.target_positions["shoulder_pan"] += self.degree_step
            print(f"[{self.prefix}] shoulder_pan: {self.target_positions['shoulder_pan']}")
        if key_state.get('shoulder_pan-'):
            self.target_positions["shoulder_pan"] -= self.degree_step
            print(f"[{self.prefix}] shoulder_pan: {self.target_positions['shoulder_pan']}")
        if key_state.get('wrist_roll+'):
            self.target_positions["wrist_roll"] += self.degree_step
            print(f"[{self.prefix}] wrist_roll: {self.target_positions['wrist_roll']}")
        if key_state.get('wrist_roll-'):
            self.target_positions["wrist_roll"] -= self.degree_step
            print(f"[{self.prefix}] wrist_roll: {self.target_positions['wrist_roll']}")
        if key_state.get('gripper+'):
            self.target_positions["gripper"] += self.degree_step
            print(f"[{self.prefix}] gripper: {self.target_positions['gripper']}")
        if key_state.get('gripper-'):
            self.target_positions["gripper"] -= self.degree_step
            print(f"[{self.prefix}] gripper: {self.target_positions['gripper']}")
        if key_state.get('pitch+'):
            self.pitch += self.degree_step
            print(f"[{self.prefix}] pitch: {self.pitch}")
        if key_state.get('pitch-'):
            self.pitch -= self.degree_step
            print(f"[{self.prefix}] pitch: {self.pitch}")

        # XY plane (IK)
        moved = False
        if key_state.get('x+'):
            self.current_x += self.xy_step
            moved = True
            print(f"[{self.prefix}] x+: {self.current_x:.4f}, y: {self.current_y:.4f}")
        if key_state.get('x-'):
            self.current_x -= self.xy_step
            moved = True
            print(f"[{self.prefix}] x-: {self.current_x:.4f}, y: {self.current_y:.4f}")
        if key_state.get('y+'):
            self.current_y += self.xy_step
            moved = True
            print(f"[{self.prefix}] x: {self.current_x:.4f}, y+: {self.current_y:.4f}")
        if key_state.get('y-'):
            self.current_y -= self.xy_step
            moved = True
            print(f"[{self.prefix}] x: {self.current_x:.4f}, y-: {self.current_y:.4f}")
        if moved:
            joint2, joint3 = self.kinematics.inverse_kinematics(self.current_x, self.current_y)
            self.target_positions["shoulder_lift"] = joint2
            self.target_positions["elbow_flex"] = joint3
            print(f"[{self.prefix}] shoulder_lift: {joint2}, elbow_flex: {joint3}")

        # Wrist flex is always coupled to pitch and the other two
        self.target_positions["wrist_flex"] = (
            -self.target_positions["shoulder_lift"]
            -self.target_positions["elbow_flex"]
            + self.pitch
        )
        # print(f"[{self.prefix}] wrist_flex: {self.target_positions['wrist_flex']}")

    def p_control_action(self, robot):
        obs = robot.get_observation()
        current = {j: obs[f"{self.prefix}_arm_{j}.pos"] for j in self.joint_map}
        action = {}
        for j in self.target_positions:
            error = self.target_positions[j] - current[j]
            control = self.kp * error
            action[f"{self.joint_map[j]}.pos"] = current[j] + control
        return action


class SmoothBaseController:
    """Simplified smooth base controller with acceleration/deceleration"""
    
    def __init__(self):
        self.current_speed = 0.0
        self.last_time = time.time()
        self.last_direction = {"x.vel": 0.0, "theta.vel": 0.0}
        self.is_moving = False
    
    def update(self, pressed_keys, robot):
        """Update smooth control and return base action"""
        current_time = time.time()
        dt = current_time - self.last_time
        self.last_time = current_time
        
        # Check if any base keys are pressed
        base_keys = [
            robot.teleop_keys['forward'],
            robot.teleop_keys['backward'], 
            robot.teleop_keys['rotate_left'],
            robot.teleop_keys['rotate_right']
        ]
        any_key_pressed = any(key in pressed_keys for key in base_keys)
        
        # Calculate base action directly (bypass robot's built-in speed control)
        base_action = {"x.vel": 0.0, "theta.vel": 0.0}
        
        if any_key_pressed:
            # Keys pressed - calculate direction and accelerate
            if not self.is_moving:
                self.is_moving = True
                print("[BASE] Starting acceleration")
            
            # Get current speed level from robot
            speed_setting = robot.speed_levels[robot.speed_index]
            linear_speed = speed_setting["linear"]  # e.g. 0.1, 0.2, or 0.3
            angular_speed = speed_setting["angular"]  # e.g. 30, 60, or 90
            
            # Calculate direction based on pressed keys
            if robot.teleop_keys["forward"] in pressed_keys:
                base_action["x.vel"] += linear_speed
            if robot.teleop_keys["backward"] in pressed_keys:
                base_action["x.vel"] -= linear_speed
            if robot.teleop_keys["rotate_left"] in pressed_keys:
                base_action["theta.vel"] += angular_speed
            if robot.teleop_keys["rotate_right"] in pressed_keys:
                base_action["theta.vel"] -= angular_speed
            
            # Store current direction for deceleration
            self.last_direction = base_action.copy()
            
            # Accelerate
            self.current_speed += BASE_ACCELERATION_RATE * dt
            self.current_speed = min(self.current_speed, BASE_MAX_SPEED)
                
        else:
            # No keys pressed - decelerate
            if self.is_moving:
                self.is_moving = False
                print("[BASE] Starting deceleration")
            
            # Use last direction for deceleration
            if self.current_speed > 0.01 and self.last_direction:
                base_action = self.last_direction.copy()
            
            # Decelerate
            self.current_speed -= BASE_DECELERATION_RATE * dt
            self.current_speed = max(self.current_speed, 0.0)
        
        # Apply speed multiplier
        if base_action:
            for key in base_action:
                if 'vel' in key:
                    original_value = base_action[key]
                    base_action[key] *= self.current_speed
                    
                    # Ensure minimum velocity during deceleration to prevent motor cutoff
                    if self.current_speed > 0.01 and abs(base_action[key]) < MIN_VELOCITY_THRESHOLD:
                        # During deceleration, maintain minimum velocity to keep motors moving
                        base_action[key] = MIN_VELOCITY_THRESHOLD if original_value > 0 else -MIN_VELOCITY_THRESHOLD
        
        # Debug output
        if any_key_pressed:
            print(f"[BASE] ACCEL: Speed={self.current_speed:.2f}, Action={base_action}")
        elif self.current_speed > 0.01:
            print(f"[BASE] DECEL: Speed={self.current_speed:.2f}, Action={base_action}")
        elif self.current_speed <= 0.01:
            print(f"[BASE] STOPPED: Speed={self.current_speed:.2f}")
        
        return base_action


# Global smooth controller instance
smooth_controller = SmoothBaseController()
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

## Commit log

2025-12-21 fix: remove manual camera setup; use utils to build dataset frame
2025-12-22 Create odrive.md for FOC control documentation
    Add initial documentation for FOC control scripts
2025-12-30 Update link for dual-wheel version release
2026-01-04 Add intro section for dual wheel version 0.4.0
    Added introductory section detailing changes in version 0.4.0, including improvements in stability, speed, and design. Discussed limitations of servo motors and future collaboration plans.
2026-01-05 Add assembly videos to 2-wheel assembly guide
    Added official assembly videos from Wowrobo to the documentation.
2026-01-07 Add refined neck.
    [XLeRobot040_neck_refined.step]
2026-01-09 Fix component dimensions and misaligned mounting holes.
2026-01-22 更新README_CN.md中的新闻部分
    更新新闻部分以包含最新信息和链接
2026-02-03 Refactor imports in keyboard joint control example
    Updated import statements for SO100 robot control.
2026-02-03 Enhance gripper control with scaling and limits
    Adjust gripper control to apply a scaling factor and limit range.
2026-02-26 readme: odrive setup
2026-02-26 files: odrive board housing
    [PCB_v3.2.step, odrive_cap.step, odrive_housing.step]
2026-02-26 file: odrive cap v2
    [odrive_cap.step]
2026-02-27 file: front/back hub
    [front_back_hub.step, odrive_motor_holder.step]
2026-02-27 file: thor holders
    [thor_holder_corner.step, thor_holder_edge.step]
2026-02-27 file: ht panthera holders
    [ht_board_holder_corner.step, ht_holder_single.step, ht_holder_single_bottom.step]

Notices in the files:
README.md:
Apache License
